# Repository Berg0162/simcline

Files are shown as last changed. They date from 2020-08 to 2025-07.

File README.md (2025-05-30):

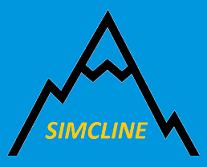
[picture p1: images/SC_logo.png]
SIMCLINE Icon
#  &nbsp; SIMCLINE for Smart TACX, Wahoo KICKR and FTMS enabled trainers
# Simulation of Changing Road Inclination for Indoor Cycling<br>
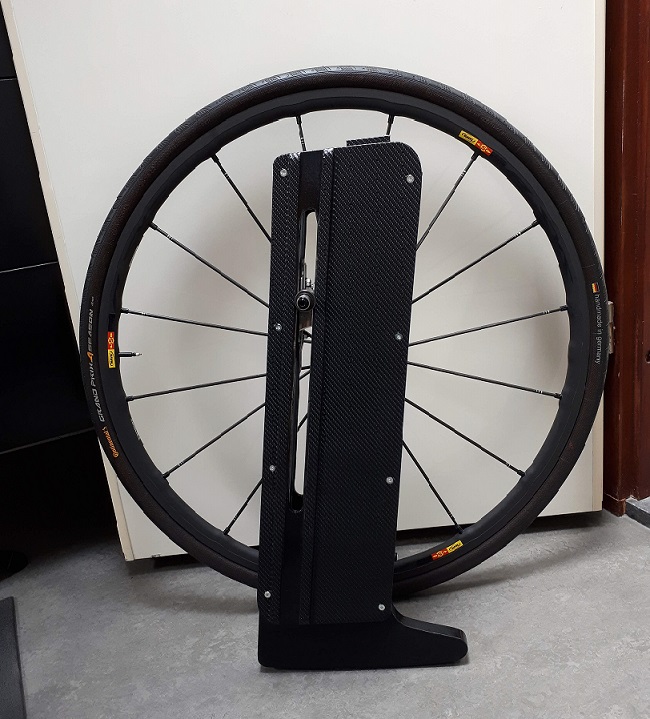
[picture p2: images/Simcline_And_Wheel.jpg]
SIMCLINE 1

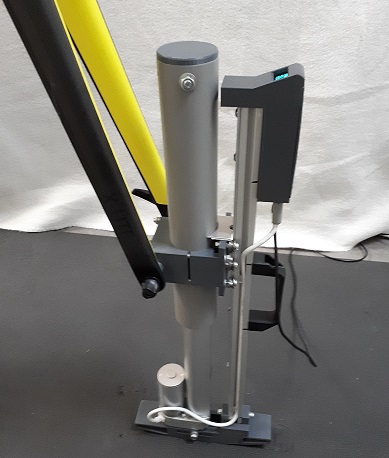
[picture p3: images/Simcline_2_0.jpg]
SIMCLINE 2

The SIMCLINE physically adjusts the bike position to mimic hilly roads, climbing and descending. This allows the rider to naturally change position on the bike, engage climbing muscles, and improve pedaling technique to become a more efficient and powerful climber.<br>
Without user intervention the SIMCLINE will replicate inclines and declines depicted in (online & offline) training programs (like <b>Zwift, Rouvy, VeloReality, myWhoosh</b> and many others) that adjust accordingly the resistance of the indoor trainer.<br>
The SIMCLINE auto connects at power up with a smart Wahoo KICKR trainer or a smart TACX trainer and let's relive the ascents and descents from favorite rides or routes while training indoors.<br>
The physical reach is: 20% maximum incline and -10% maximum decline. However, the reach that the rider is comfortable with can be adjusted!<br>
The SIMCLINE pairs directly to the smart trainer and with your PC/Laptop with (Zwift) training App for a connection that notifies the SIMCLINE to simulate autonomous the (change in) physical grade of the road during an indoor ride.<br>
During operation an OLED display shows the road grade in digits and in graphics.<br>
The SIMCLINE Companion App (for Android smartphones) can be paired, only when the training App is disconnected, for adjusting operational settings, like Ascent Grade Limit (between 0-20%), Descent Grade Limit (between 0-10%), Road Grade Change Factor (between 0-100%) and manual Up and Down control. Notice that the Companion App has a slightly different functionality depending of what brand of trainer (TACX or Wahoo) is connected, due to specific connectivity differences. <br clear="left"> 
<br>
There are <b>Instructables</b> available with all the nitty gritty of how to create, construct and install the various parts and components of the different SIMCLINE versions.<br>

# [Mechanical SIMCLINE version 1.0](https://www.instructables.com/id/SIMCLINE-Simulation-of-Changing-Road-Incline-for-I/)<br>
# [Mechanical SIMCLINE version 2.0](https://www.instructables.com/SIMCLINE-20-Easy-Simulation-of-Road-Incline/)<br>

The applied electronic components in the 2 projects are somewhat different but NOT in an essential way, as documented hereafter.<br>
<b>NOTICE that the SIMCLINE control code can be run with both (mechanically different) SIMCLINE versions!</b> However, 3 different code versions are specially designed for operating with a TACX <b>or</b> Wahoo Kickr <b>or</b> FTMS enabled trainers!</b> You will find in the arduino folder all the test programs and the common libraries. These will help you to test the electronic components separately and built together of both SIMCLINE versions.<br> 

Finally you have to select the SIMCLINE code that is appropriate for the trainer of your liking!<br>

# [nRF52/ESP32 support for Legacy Smart TACX trainers](https://github.com/Berg0162/simcline/tree/master/Tacx%20Smart)<br>

# [nRF52/ESP32 support for Legacy Wahoo KICKR trainers](https://github.com/Berg0162/simcline/tree/master/Wahoo%20Kickr/)<br>

# [nRF52 support for Modern FTMS enabled trainers](https://github.com/Berg0162/simcline/tree/master/FTMS%20Enabled/)<br>

# [ESP32 support for Modern FTMS enabled trainers: Simcline-V2](https://github.com/Berg0162/Simcline-V2)<br>

# Mechanical SIMCLINE 1.0<br>
See: Instructables [SIMCLINE 1.0 Instructables](https://www.instructables.com/id/SIMCLINE-Simulation-of-Changing-Road-Incline-for-I/)
<br clear="left">

# Electronic Components and Circuitry used in version 1.0<br>
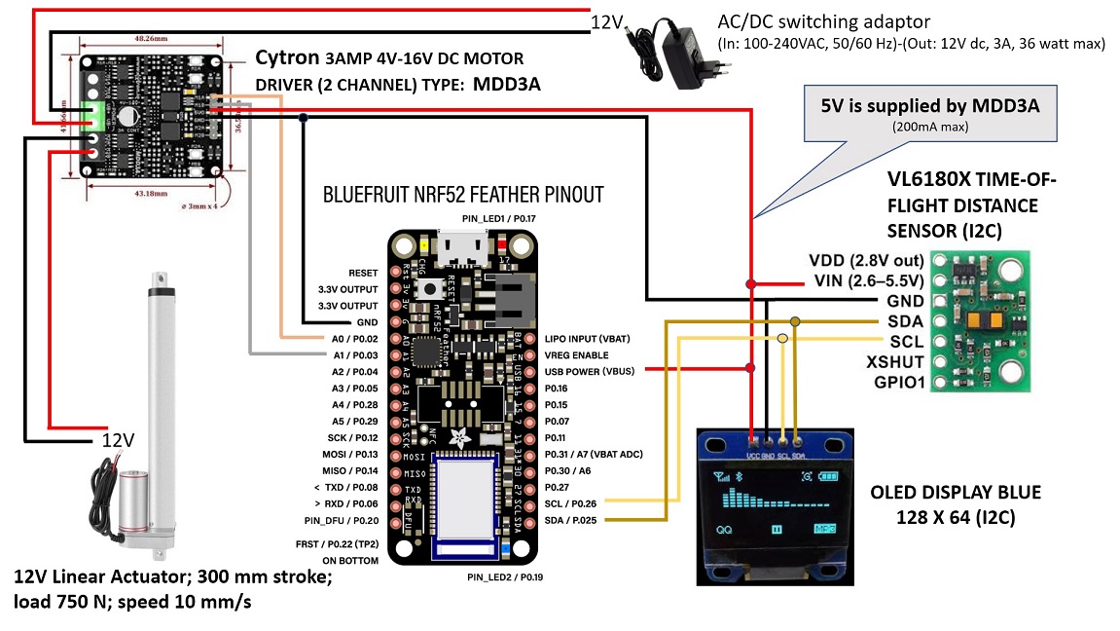
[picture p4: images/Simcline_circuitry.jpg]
Circuitry version 1.0

The original project has been elaborated with different electronic parts than the later version. I have then chosen for the following 4 active components: <br>
<b>Cytron Motor Driver MDD3A.</b> Two channel motor driver for 12 V and 3 Amperes with buttons to test manually the working of the attached DC motor. This board enables the processor to set the Actuator motor in up or down movement. It transforms logical digital levels (Go Up, Go Down and Stop) from the Feather nRF52/ESP32 to switching of 12 Volt at 3 Amperes max., the levels at which the Actuator works.<br>
<b>Adafruit Feather nRF52840 Express</b><br>
Is another easy-to-use all-in-one Bluetooth Low Energy board with a native-Bluetooth chip, the nRF52840! Notice that the Feather nRF52840 Express is to be prefered and has better value for money! It's Adafruits's take on an 'all-in-one' Arduino-compatible + Bluetooth Low Energy with built in USB and battery charging. It is a low power, handsome and fast processor board with lots of memory and I/O pins. Can easily be programmed over the USB connection. <br>
<b>Adafruit HUZZAH32 ESP32 Feather V2</b><br>
Recently we have shared Simcline code that is targeted for another of the Adafruit star Feathers: the <b>Adafruit HUZZAH32 ESP32 Feather V2</b> - with the fabulous ESP32 WROOM module. The ESP32 has both WiFi and Bluetooth Classic/LE support. The new HUZZAH32 V2 is Adafruit's redesigned ESP32-based Feather V2. Compared to the original Feather with only 4 MB Flash and no PSRAM, the V2 has 8 MB Flash and 2 MB PSRAM. Packed with everything people love about Feathers: built in USB-to-Serial converter, automatic bootloader reset, Lithium Ion/Polymer charger, and just about all of the GPIOs brought out.<br>
The programmed Feather nRF52/ESP32 is communicating with (a) the trainer to collect power output  information and (b) with the training App for resistance settings (like grade) or (c) with the Companion App on your mobile phone. The programmed Feather nRF52/ESP32 is in full control of the Simcline operation.<br>

<b>OLED display blue 128x64 pixels</b><br>
Small display with screen of: 25 mm x 19 mm. Shows cycling data and diagnostic info that is gathered during operation by the programmed Feather nRF52/ESP32 to inform the Simcline user about relevant information. NOTICE: Install Straight Pin Through Hole Male PCB Header on the board; these will allow later flat mounting of the board on top of the frame!<br>
<b>Time-of-Flight-Distance sensor VL6180X</b><br>
The sensor contains a very tiny laser source, and a matching sensor. The VL6180X can detect the "time of flight", or how long the laser light has taken to bounce back to the sensor. Since it uses a very narrow light source, it is perfect for determining distance of only the surface directly in front of it. The sensor registers quite accurately the (change in) position of the wheel axle during operation, by measuring the distance between the top of the inner frame and the reflection plate that is mounted on the carriage. The distance feedback of the sensor is crucial for determining how to set the position of the carriage and axle in accordance with the grade information that for example Zwift is using to set the resistance of the trainer. NOTICE: Install Right Angle Through Hole Male PCB Header Pins on the board.<br>
In retrospect I do not regret the component choices made. All components are documented very well. There are lots of examples for use in an Arduino enviroment. They have turned out to be very reliable.<br clear="left">

# Mechanical SIMCLINE 2.0<br>
See: Instructables [SIMCLINE 2.0 Instructables](https://www.instructables.com/SIMCLINE-20-Easy-Simulation-of-Road-Incline/)
<br clear="left">

# Electronic Components and Circuitry used in version 2.0<br>
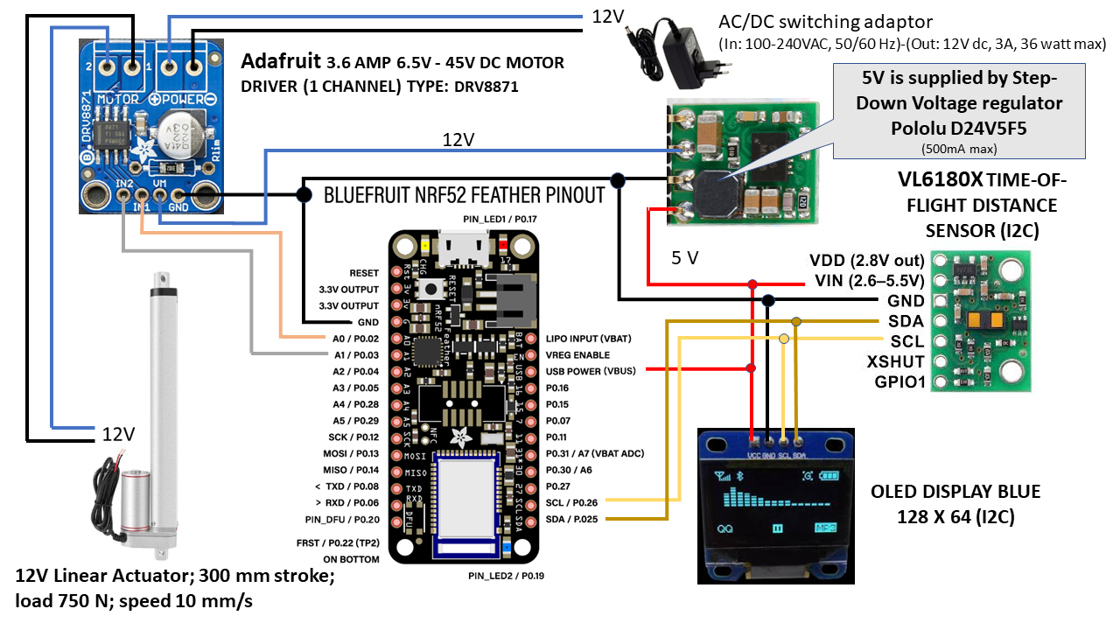
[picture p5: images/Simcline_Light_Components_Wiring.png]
Circuitry version 2.0

I have chosen for the following 5 compact active components that are slightly different from the earlier SIMCLINE project and that can finally all be mounted inside the components box:<br>
<b>Adafruit DRV8871 DC Motor Driver</b><br>
A small one channel motor driver for 12 V (6.5 - 48 V) and 3,6 Amperes max. This board enables the processor to set the Actuator motor in up or down movement. It transforms logical digital levels (Go Up, Go Down and Stop) from the Feather nRF52/ESP32 to switching of 12 Volt at 3,6 Amperes max., the levels at which the Actuator works. Notice that default the board comes limited to 2,6 Amperes and you need to add a resistor to set for max current level. Install Vertical Through Hole Male PCB Header Pins on the board; this will allow correct mounting of the board inside the components box!<br>
<b>Adafruit Feather nRF52840 Express</b><br>
Is another easy-to-use all-in-one Bluetooth Low Energy board with a native-Bluetooth chip, the nRF52840! Notice that the Feather nRF52840 Express is to be preferred and has better value for money! It's Adafruit's take on an 'all-in-one' Arduino-compatible + Bluetooth Low Energy with built in USB and battery charging. It is a low power, handsome and fast processor board with lots of memory and I/O pins. Can easily be programmed over the USB connection.<br>
<b>Adafruit HUZZAH32 ESP32 Feather V2</b><br>
Recently we have shared Simcline code that is targeted for another of the Adafruit star Feathers: the <b>Adafruit HUZZAH32 ESP32 Feather V2</b> - with the fabulous ESP32 WROOM module. The ESP32 has both WiFi and Bluetooth Classic/LE support. The new HUZZAH32 V2 is Adafruit's redesigned ESP32-based Feather V2. Compared to the original Feather with only 4 MB Flash and no PSRAM, the V2 has 8 MB Flash and 2 MB PSRAM. Packed with everything people love about Feathers: built in USB-to-Serial converter, automatic bootloader reset, Lithium Ion/Polymer charger, and just about all of the GPIOs brought out.<br>
The programmed Feather nRF52/ESP32 is communicating with (a) the trainer to collect power output  information and (b) with the training App for resistance settings (like grade) or (c) with the Companion App on your mobile phone. The programmed Feather nRF52/ESP32 is in full control of the Simcline operation.<br>

<b>OLED display blue/white 128x64 pixels (0,96 Inch, I2C)</b><br>
Small display board has a critical overall board size of 25 mm * 27 mm (!); (See for example: [Webshop](https://www.pcboard.ca/oled-128x64)). Display area itself is: 25 mm x 14 mm. Shows cycling data and diagnostic info that is gathered during operation by the Feather nRF52/ESP32 to inform the SIMCLINE user about relevant information. NOTICE: a) Many different formfactors are offered at webshops; b) Install Vertical Through Hole Male PCB Header Pins on the board; this will allow correct mounting of the board inside the components box!<br>
<b>Pololu Time-of-Flight-Distance sensor VL6180X</b><br> The sensor board (12.7 * 17.8 mm) contains a very tiny laser source, and a matching sensor. The VL6180X can detect the "time of flight", or how long the laser light has taken to bounce back to the sensor. Since it uses a very narrow light source, it is perfect for determining distance of only the surface directly in front of it. The sensor registers quite accurately the (change in) position of the wheel axle during operation, by measuring the distance between the top of the inner frame and the reflection plate that is mounted on the carriage. The distance feedback of the sensor is crucial for determining how to set the position of the carriage and axle in accordance with the grade information that for example Zwift is using to set the resistance of the trainer. NOTICE: a) VL6180X boards are also offered by different suppliers and have different formfactors; b) Install Straight Angle Through Hole Male PCB Header Pins on the board; this will allow later flat mounting of the sensor board in the components box!<br>
<b>Pololu D24V5F5</b><br>
This is a small 5V, 500mA Step-Down Voltage Regulator that is responsible for voltage conversion from 12V to 5V, the power supply for all components boards. NOTICE: Install Straight Angle Through Hole Male PCB Header Pins on the board; this will allow later easy mounting of the sensor board in the components box!<br>

All components are documented very well and are low cost. There are lots of examples for use in an Arduino environment. They have turned out to be very reliable. The exact wiring of the components can be followed in the figure above.<br>

# How Zwift, Trainer and Simcline are handling (changes in) road grade during your ride!<br>
1) The trainer calculates the resistance, among others using road grade information. That's why Zwift sends modified road grades to the trainer to set resistance. Simple as that! However, resistance (i.e. road grade) is also dependent of Zwift's famous difficulty setting. With the default difficulty setting of 50%, Zwift sends only half the value of the road grade to the trainer. Only when the Zwift App difficulty setting is 100%, Zwift will send unmodified road grades to the trainer (WYSIWYG). As a consequence the Simcline will lift accordingly and show the road grade values on the display! If you observe deviations when riding long and steady climbs, like Alpe-de-Huez or Mt-Ventoux, check the Zwift App "difficulty setting" that is most likely the cause! Most Zwifters have set the Zwift difficulty at 100%, because they want a "road-realistic" experience when training and racing indoors with Zwift.
2) Trainers do NOT react momentarily, but delayed on changes in road grade, they need to process incoming info and the (direct) drive mechanism has to be settled accordingly before you will feel it as a change in resistance. The delay between the initial command (by Zwift) and the feel on the bike is 1 to 1.5 seconds. To accommodate for this delay, the Zwift app sends commands 1 to 1.5 second <b>earlier</b> (!) than what you observe on your screen (slope of the road you see and the displayed road grade value on the Zwift window). This explains temporarily deviating values on the Simcline display in comparison what you see on the Zwift window, after all Simcline is a MITM and is the first to receive changes in road grade, to react (moving the lift mechanism) and to show the new value on the display. When riding rolling hills in rapid succession, like Zwift's Titans Grove, this is most visible! Notice that the Simcline's responsiveness is benefiting of the feature!
3) Zwift handles downhill roads differently! When the road grade values become negative, during a downhill section of the road, Zwift will consequently send only half of the road grade value to the trainer (i.e Simcline). Modern trainers with direct drive are capable to accelerate proportionally with negative road grades. So when the Zwift window shows a -8.0 grade value it has sent only -4.0 road grade to the trainer. The rationale behind this is to minimize effortless riding, after all you get on an indoor bike to do some work! Simcline will act accordingly and display only 50% of the Zwift road grade value on downhill sections!  
4) After Zwift has paired with your trainer it sends a first road grade value (randomly between 2.0 and 5.0) to the trainer, to wake-up/activate the resistance mechanism. You will feel the resistance while you were expecting a flat road for a start. Simcline, being a MITM, will lift your front wheel accordingly! This road grade value remains constant, until you have actually <b>started</b> with the ride of your choice!
5) The Simcline code has its own setting that influences how it will react on and display the road grade value sent by Zwift. The Grade-Change-Factor functionality was originally designed and implemented to allow a Simcline user to attenuate the actuator movements in case of a noisy and/or slow actuator. Notice that the original (unmodified) Zwift grade value is passed on to the trainer, so the trainer's resistance is NOT affected by the Grade-Change-Factor setting! Default code setting for the Grade-Change-Factor is 100% and it can be modified dynamically using the Simcline app.

In conclusion when you see different road grade values in the Zwift window compared with the Simcline display, this can have different reasons! If you consider this a problem: check first Zwift difficulty setting and Grade-Change-Factor of the Simcline, these can be modified to what you prefer! Like it or not, the other causes are Zwift features and part of the design! Cycling Apps like Rouvy and MyWhoosh handle road grades more or less comparably.

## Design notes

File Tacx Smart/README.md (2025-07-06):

# SIMCLINE Icon &nbsp; SIMCLINE for TACX
# Simulation of Changing Road Inclination for Indoor Cycling <br>
SIMCLINE
SIMCLINE 2
The SIMCLINE physically adjusts the bike position to mimic hilly roads, climbing and descending. This allows the rider to naturally change position on the bike, engage climbing muscles, and improve pedaling technique to become a more efficient and powerful climber.<br>
Without user intervention the SIMCLINE will replicate inclines and declines depicted in (online & offline) training programs (like Zwift, Rouvy, VeloReality and many others) that adjust accordingly the resistance of the indoor trainer.<br>
The SIMCLINE auto connects at power up with a smart TACX trainer and let's relive the ascents and descents from favorite rides or routes while training indoors.<br>
The physical reach is: 20% maximum incline and -10% maximum decline. However, the reach that the rider is comfortable with can be adjusted even during a ride!<br>
The SIMCLINE pairs directly to the TACX smart trainer for a connection that notifies the SIMCLINE to simulate autonomous the (change in) physical grade of the road during an indoor ride.<br>
During operation an OLED display shows the road grade in digits and in graphics or cycling data from the trainer (speed, power, cadence, elapsed time and distance).<br>
The SIMCLINE Companion App (for Android smartphones) can be paired simultaneously for adjusting operational settings, like Ascent Grade Limit (between 0-20%) and Descent Grade Limit (between 0-10%), Road Grade Change Factor (between 0-100%) and the type of OLED display format.<br clear="left"> 

# Choose a Development board: nRF52840 or ESP32?<br>
Until early 2023 the Simcline project (a.o.) solely worked with the <b>Feather nRF52840 Express</b> development board and the Bluefruit/Adafruit libraries. This is a very stable platform and gave reliable results during development and what's more during many indoor seasons of 5 hours per week operation! However, the MITM application and actuator control (a.k.a. Simcline) is at the capacity limits of the nRF52840 processor. 
See for a reliable and <b>proven</b> solution: [Adafruit Feather nRF52840 Express](https://learn.adafruit.com/introducing-the-adafruit-nrf52840-feather) <br>

So the question was raised why not use the <b>ESP32</b>, a series of low-cost and low-power System on a Chip (SoC) microcontrollers developed by Espressif that include Wi-Fi and Bluetooth wireless capabilities and dual-core processor? See for an introduction: [Random Nerds Tutorials](https://randomnerdtutorials.com/getting-started-with-esp32/). Particularly the multiprocessing capabilities of the dual-core processor make the ESP32 a very tempting option in this project!
To benefit of the same formfactor (fit with the Simcline 2.0 component box!), I decided to (re)produce the Simcline code with the [Adafruit Feather ESP32 V2](https://learn.adafruit.com/adafruit-esp32-feather-v2) for the <b>ESP32</b> platform. Just comparing the overal specs (on paper) of both processor platforms is not sufficient... one needs to take into account the (quality of the) available libraries as well to reach success. The 'standard' ESP32 Arduino <b>Bluedroid</b> library (for BLE support) turned out to be buggy! Fortunately [H2Zero](https://github.com/h2zero/NimBLE-Arduino) has created a more or less compatible replacement for Bluedroid, called <b>NimBLE-Arduino</b>! The application of <b>NimBLE</b> saved the porting of the software to the ESP32 platform! 
In week 10 of 2023 the ESP32 code reached a stable level and became publicly available for testing with Tacx-trainers.

# How to start?<br>
+ Install the [Arduino IDE](https://www.arduino.cc/en/Main/Software) and all the libraries on a PC/Mac.
+ If you are using an ESP32 board then also download the ESP32 NimBLE library, see [Arduino Installation NimBLE](https://github.com/h2zero/NimBLE-Arduino#arduino-installation)
+ Download all the code from [Github](https://github.com/Berg0162/simcline/tree/master/Tacx%20Smart) and install.
<br>
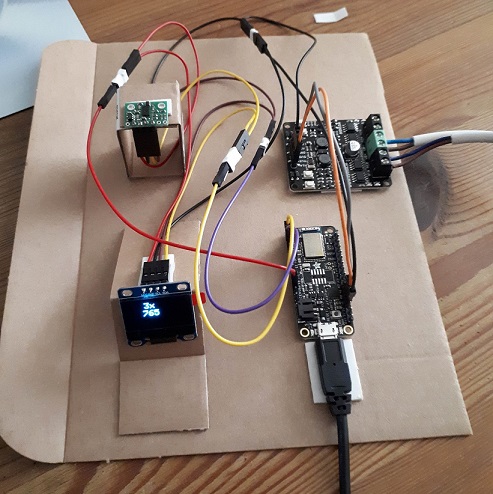
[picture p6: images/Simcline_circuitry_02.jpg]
Cardboard

When I started the project in 2020 I did not have any practical experience with any of the components. So I had to setup the circuitry step by step adding components and did a lot of time consuming but instructive testing first. My advice is to setup the electronic components first in a similar way as shown on the photo with the cardboard base. Use double sided adhesive tape but only attach it on sections that have no pcb-wiring or soldering, to avoid possible electrical interference. You will find in this Github repository all the code that controls the Simcline and the Arduino test programs (modified for this project) that focus on components seperately and in conjunction.<br clear="left">

# ANT+, FE-C protocol and BLE<br>
It took me a lot of time exploring the relevant techniques, protocols and software tools involved with ANT+, BLE and FE-C to acquire the approriate knowledge. Many projects at Github address ANT+ and/or BLE with a different point of departure, however I have learnt a lot of looking closely at the many program codes, explanations and descriptions. Finally, I tracked down how a smart up/down lift of my front wheel axle is optimally benefitting from the (ANT+) FE-C protocol when I am indoor riding with the TACX Neo in the hilly Zwift game world or with any other virtual cycling program that simulates road grade. After a succesfull proof of concept with ANT+ and BLE tools (see [ThisisANT Tools](https://www.thisisant.com/developer/resources/software-tools/) and [Nordic NRF Connect](https://www.nordicsemi.com/Software-and-tools/Development-Tools/nRF-Connect-for-mobile). I was convinced to bring the project to a successful conclusion!
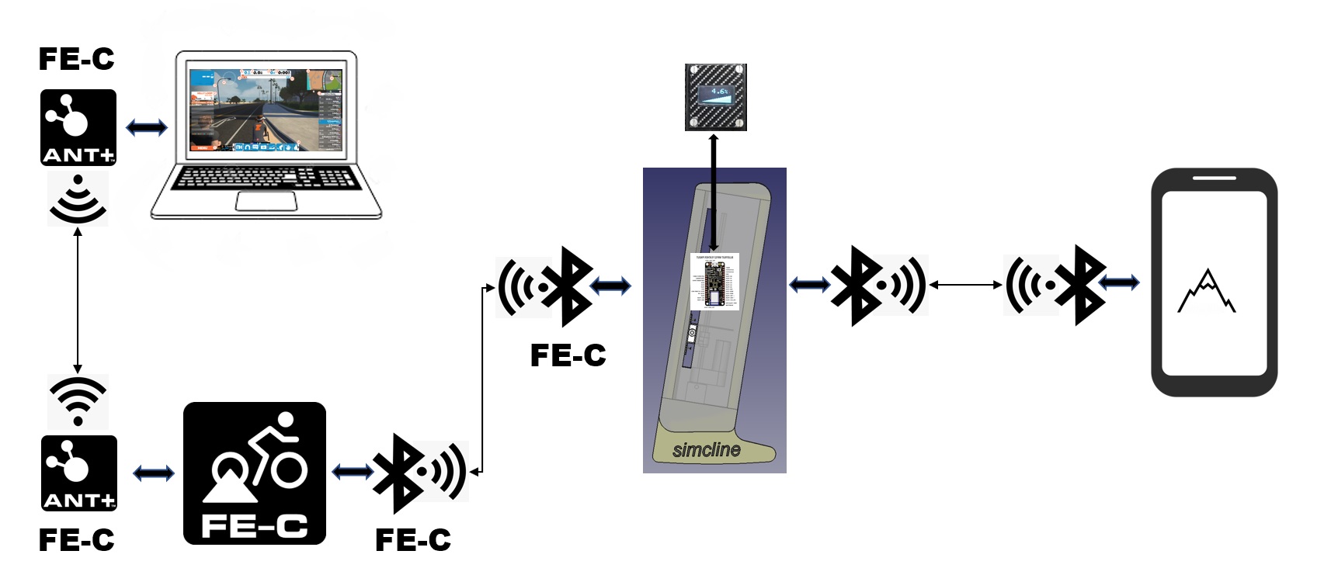
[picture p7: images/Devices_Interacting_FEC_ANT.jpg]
FE-C
<br clear="left">
<b>ANT+ Trainer Control (FE-C)</b><br>
The ANT+ FE-C protocol details the bi-directional message communication of trainer data (speed, power, etcetera) from trainer to the controller and from the controller to the trainer commands or settings of targeted power, trainer resistance (grade) and calibration controls. See [ThisisAnt](http://www.thisisant.com/) for all conceivable documentation, tools, implementations, ANT+ based products, etcetera! See at Github for a detailed description of the [ANT Message Protocol and Usage](https://github.com/Berg0162/simcline/blob/master/docs/ANT_Message_Protocol_and_Usage_Rev_5.1.pdf).
The majority of FE-C trainers on the market is dual ANT+ & Bluetooth Smart in some capacity. The Tacx Neo generation has full capacity: ANT+ Trainer Control (FE-C) and Bluetooth Smart.<br>
Tacx published in 2015 a document [TACX, FE-C and Bluetooth](https://github.com/Berg0162/simcline/blob/master/docs/How_to_FE_C_over_BLE_v1_0_0.pdf) that explains how to use the FE-C ANT+ protocol over BLE feature implemented on all Tacx Smart Trainers then: `Genius Smart, Bushido Smart, Vortex Smart, Flow Smart, Satori Smart and NEO`. Tacx designed this feature because at that time an open standard (on BLE) for trainers was lacking. <b>Always check if your trainer has support for the FE-C ANT+ protocol over BLE feature, since NOT all TACX Smart Trainers that are labelled smart are equally smart!</b>
Now there is (<b>FTMS</b>) FiTness Machine Service protocol to control fitness equipment over Bluetooth. According to the smart trainer recommendations guide winter 2019-2020 of [DCRainmaker](https://www.dcrainmaker.com/2019/10/the-smart-trainer-recommendations-guide-winter-2019-2020.html) the situation evolved:
> Meanwhile, for Bluetooth Smart, there’s FTMS, which is basically the same thing as FE-C when it comes to trainers. It’s not quite as widely adopted yet by trainer companies, but is by app companies. On the trainer company side only Elite, Saris, and Kinetic support it across the board. With Tacx having it on some but not all units, and Wahoo having it on no units (but all Wahoo and Tacx trainers support private Bluetooth Smart with all major apps anyway).<br>

<b>FE-C over Bluetooth</b><br>
In the document Tacx described how Tacx Smart trainers use an ANT+ FE-C definition for the data content, but transports this data over a BLE serial port service. The prerequisite that remains for this technique is thourough knowledge of ANT+ <b>AND</b> the ANT+ FE-C protocol. A complete description of FE-C can be found here at [Github](https://github.com/Berg0162/simcline/blob/master/docs/ANT+_Device_Profile_Fitness_Equipment_Rev_5.0.pdf).<br>
<b>Nordic Serial Port Service</b><br>
The transport method that is used is derived from the Nordic Uart Service. This serial port service can basically send and receive arrays of data ranging from 1..20 bytes. The only difference is the service UUID and the two characteristics UUID’s. These are renamed conforming the internal Tacx standard UUID with the specific part for the FE-C service starting with 0xFEC.<br>
<b>ANT+ and BLE Roles</b><br>
The Adafruit Feather nRF52 Express is equiped with a native-Bluetooth chip, the nRF52840 of Nordic Semiconductor. This chip can be loaded with "SoftDevices" for different applications. Nordic nRF52 and nRF51 Series support ANT+ and ANT+ / Bluetooth LE SoftDevices. However, the adafruit version is loaded with SoftDevice S132: a high-performance Bluetooth Low Energy protocol stack for the nRF52840 System-on-Chips (SoCs). It supports up to 20 concurrent links in all roles (Broadcaster, <b>Central</b>, Observer, <b>Peripheral</b>). It is Bluetooth 5.1 qualified and supports the following Bluetooth features: high-throughput 2 Mbps, Advertising Extensions and channel selection algorithms. <br>
> Recently we have shared Simcline code that is targeted for another of the Adafruit star Feathers: the <b>Adafruit HUZZAH32 ESP32 Feather V2</b> - with the fabulous ESP32 WROOM module. The ESP32 has both WiFi and Bluetooth Classic/LE support. The new HUZZAH32 V2 is Adafruit's redesigned ESP32-based Feather V2. Compared to the original Feather with only 4 MB Flash and no PSRAM, the V2 has 8 MB Flash and 2 MB PSRAM. Packed with everything people love about Feathers: built in USB-to-Serial converter, automatic bootloader reset, Lithium Ion/Polymer charger, and just about all of the GPIOs brought out.<br>

In our design the SIMCLINE has a <b>Central</b> and as well as a <b>Peripheral</b> role simultaneously. The communication SIMCLINE to Trainer is Central to Peripheral respectively and the communication SIMCLINE to Smartphone is Peripheral to Central. The peripheral BLE Device is advertising its name, services and characteristics and the central device is deciding to connect and control the communication. <br>
The communication between the trainer (<b>controllable</b>) and the PC/MAC/Tablet-application (<b>controller</b>, like Zwift) is full blown ANT+ and complies the FE-C protocol. The SIMCLINE is not interfering with this setup in any way! The application on PC/MAC/Tablet is <b>controller</b> and remains in full and only charge of setting the trainers resistance.<br>
<b>How to detect the grade of the simulated track?</b><br>
The SIMCLINE is paired with the trainer over a different channel: Bluetooth! In that configuration it is complying to the ANT+ FE-C protocol as well but over Bluetooth LE. The trainer is not only broadcasting FE-C messages with cycling data (speed, cadence, power, etcetera) over ANT+ to the <b>controller</b>-application (like Zwift), but also over the BLE connection to the paired Feather nRF52/ESP32. The program of the Feather nRF52/ESP32 is dealing with these data in its own way, independent of the <b>ANT+ controller</b>-application.
At regular intervals the Feather nRF52/ESP32 is programmed to send a socalled Common Page 70 (0x46) (Request Data Page) with the request data page field set to Data Page <b>51</b>.
```C++
.
//Define the FE-C ANT+ Common Page 70 with Request for Page #51
const unsigned char Page51Bytes[13] = {
    0xA4, //Sync
    0x09, //Length
    0x4F, //Acknowledge message type
    0x05, //Channel 
          //Data
    0x46, //Common Page 70
    0xFF,
    0xFF,
    0xFF, //Descriptor byte 1 (0xFF for no value)
    0xFF, //Descriptor byte 2 (0xFF for no value)
    0x80, //Requested transmission response
    0x33, //Requested Page number 51 
    0x01, //Command type (0x01 for request data page, 0x02 for request ANT-FS session)
    0x47}; //Checksum;
.
```
Sending Common Page 70 allows a connected device to request specific data pages from the trainer. The trainer replies with Common Page 71 (0x47) (Command Status) to the requester, the Feather nRF52/ESP32. The purpose of the command status page is to confirm the status of commands (and settings) sent from a controller to the controllable trainer. The last <b>settings</b> of the Data Page 51 (0x33) (Track Resistance) are included in the data of Common Page 71. The Track Resistance Page itself is sent by the controller (like Zwift) to command the trainer to use simulation mode, and to set the desired track resistance factors. It provides the simulation parameters for the trainer, the rolling resistance and gravitational resistance applied to the rider. <br>
```C++
.
#endif
  // Standard FE-C Data Message Format
  // buffer[0]  ->  Sync
  // buffer[1]  ->  Msg Length
  // buffer[2]  ->  Msg ID
  // buffer[3]  ->  Channel Number
  // buffer[4]-buffer[12] Payload of 8 bytes --> buffer[4] is byte(0) of Payload bytes 
  // buffer[13] ->  Checksum
  // --------------------------------
  uint8_t DataPageNumber = buffer[4]; // Get Data Page Number from ANT FE-C packet
  // process only the data pages we are interested in, ignore others !
  switch(DataPageNumber) {
    ///////////////////////////////////////////////////////////////
    //////////////////// Handle PAGE 71 ///////////////////////////
    ////////////// Requested PAGE 51 for grade info ///////////////
    //At a regular rate Page 51 is requested for, so process here//
    ///////////////////////////////////////////////////////////////
    case 0x47 :
    // buffer[4] -> Contains 71 (0x47) -> Common Page 71 -> Command status
    // buffer[5] -> Last Received Command ID
    // buffer[6] -> Sequence #
    // buffer[7] -> Command Status
    // buffer[8]-buffer[12] -> Response data 5 bytes
    // buffer[13] -> Checksum
    if ( buffer[5] == 0x33 ) { // check for Requested Page 51
      // We are interested in the Requested Page 51 (0x33) --> Track Resistance
      // in that case the packet contains:
      // buffer[5] -> Last Received Command ID --> Data Page Number 51 (0x33)
      // buffer[6] -> Reserved and set to 0xFF
      // buffer[7] -> Reserved and set to 0xFF
      // buffer[8] -> Reserved and set to 0xFF
      // buffer[9]-buffer[12] -> Response data 4 bytes
      // buffer[13] -> Checksum
      uint8_t lsb_GradeValue = buffer[9]; // Grade (Slope) LSB
      uint8_t msb_GradeValue = buffer[10];// Grade (Slope) MSB
      RawgradeValue = lsb_GradeValue + msb_GradeValue*256;
      // buffer[11] -> Coefficient of Rolling Resistance
.
```
By sending regularly a request for Data Page 51 (0x33) (Track Resistance) the SIMCLINE is always informed about the settings of the current grade of the simulated track and the coefficient of rolling resistance. These values are both set by the <b>ANT+ controller</b>. For proper functioning of the SIMCLINE only the current road grade is critical.</br>

# Dual Processor use with ESP32
One of the advantages of the ESP32 platform is the fact that the ESP32 WROOM processor has two cores. This makes it possible to precisely balance the load of a program over 2 processor cores. <br>
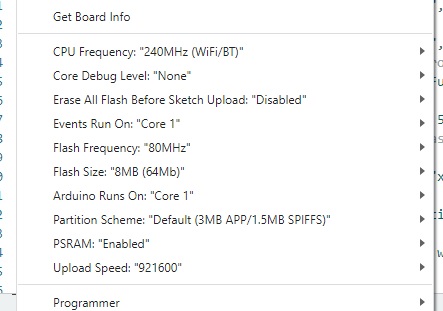
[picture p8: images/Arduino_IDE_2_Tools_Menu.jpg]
Arduino IDE 2.0 Tools Menu

With the Simcline this is particular usefull for the motor control of the actuator. During operation Zwift sends from time to time new settings, and one of these is the grade value (road inclination in degrees). The program translates the grade to a level that should be reached by the actuator to simulate exactly the road grade that was received from Zwift. However, the actuator can only be switched to <b>move up</b>, <b>move down</b> or <b>stop</b>. After  having set the actuator to move (up or down), the program has to check continuously if the actuator has reached the desired level by reading its position with the help of the Time-Of-Flight sensor and act accordingly. Meanwhile the trainer sends your cycling data and the Zwift app has to confirm the receipt of these data. The data sent by Zwift has also to be tranferred to the trainer and also the trainer has to confirm the receipt. Being a MITM means handling a lot of BLE traffic and it does not allow for mistakes!
The load of the Simcline program itself, the BLE handling and the critical control of the actuator is balanced over 2 processor cores on the ESP32 platform.
The following code snippets show how this is achieved for controlling the actuator motor. To avoid conflicts during variable updates (i.c. TargetPosition) a Binary Semaphore scheme is applied to protect <b>task shared variables</b> during an update.<br clear="left">

At the start the major players are defined
```C++
.
// ----------------------xControlUpDownMovement task definitions ------------------
SemaphoreHandle_t xSemaphore = NULL;
TaskHandle_t ControlTaskHandle = NULL;
// Set Arduino IDE Tools Menu --> Events Run On: "Core 1"
// Set Arduino IDE Tools Menu --> Arduino Runs On: "Core 1"
// Run xControlUpDownMovement on "Core 0"
const BaseType_t xControlCoreID = 0;
void xControlUpDownMovement(void* arg); 
// --------------------------------------------------------------------------------
.
```
In the setup() routine the variables are instantiated (after checking the mechanics of the motor function) and the <b>xControlUpDownMovement</b> task is pinned to processor <b>core 0</b>, with a priority of 10. Most of the Simcline program and Events are running on <b>core 1</b>.
```C++
.
  } else {
    ShowOnOledLarge("Testing", "Functions", "Done!", 500);
    // Is working properly --> Start Motor Control Task
    xSemaphore = xSemaphoreCreateBinary();
    xTaskCreatePinnedToCore(xControlUpDownMovement, "xControlUpDownMovement", 4096, NULL, 10, &ControlTaskHandle, xControlCoreID);
    xSemaphoreGive(xSemaphore);
    DEBUG_PRINTLN("Motor Control Task Created and Active!");        
    IsBasicMotorFunctions = true;
    DEBUG_PRINTLN("Simcline Basic Motor Funtions are working!!");
    // Put Simcline in neutral: flat road position
#ifdef EMA_ALPHA
    // Init EMA filter at first call with flat road position as reference
    TargetPosition = EMA_TargetPositionFilter(TargetPosition); 
#endif
    SetNewActuatorPosition();
  }
.
```
Whenever new values for the road grade are received these are translated to a physical actuator position (level above ground) and the <b>TargetPosition</b> is set during Semaphore protection. When the new position has been set, the protection is cancelled, and the motor control task can access the new setting.
```C++
.
void SetNewActuatorPosition(void) {
  // Handle mechanical movement i.e. wheel position in accordance with Road Inclination
  // Map RawgradeValue ranging from 0 to 40.000 on the
  // TargetPosition (between MINPOSITION and MAXPOSITION) of the Lifter
  // Notice 22000 is equivalent to +20% incline and 19000 to -10% incline
  RawgradeValue = constrain(RawgradeValue, RGVMIN, RGVMAX); // Keep values within the safe range
  TargetPosition = map(RawgradeValue, RGVMIN, RGVMAX, MAXPOSITION, MINPOSITION);
  // EMA filter for smoothing quickly fluctuating Target Position values see: Zwift Titan Grove
#ifdef EMA_ALPHA
  TargetPosition = EMA_TargetPositionFilter(TargetPosition);
#endif
  if(IsBasicMotorFunctions) {  
    xSemaphoreTake(xSemaphore, portMAX_DELAY); 
    lift.SetTargetPosition(TargetPosition);
    xSemaphoreGive(xSemaphore);
#ifdef MOVEMENTDEBUG
    DEBUG_PRINTF("RawgradeValue: %05d Grade percent: %03.1f%% ", RawgradeValue, gradePercentValue);
    DEBUG_PRINTF("TargetPosition: %03d\n", TargetPosition, DEC);
#endif
  }  
}
.
```
The motor control task regularly checks how far off the actuator position is from its target position and if it should be braked yet. However, it happens all the time that the road grade changed from upward to flat or to downward. The actuator should follow these changes and therefore the motor is switched many times to brake or to reverse its movement. When the motor control task is accessing the relevant variables the semaphore is protecting these against updates!
```C++
void xControlUpDownMovement(void *arg) {
  // Check "continuously" the Actuator Position and move Motor Up/Down until target position is reached
  int OnOffsetAction = 0;
  const TickType_t xDelay = 110 / portTICK_PERIOD_MS; // Block for 110ms < 10Hz sample rate of VL6180X
  while(1) {
    if(xSemaphoreTake(xSemaphore, portMAX_DELAY)) {
        // BLE channels can interrupt and consequently target position changes on-the-fly !!
        // We do not want changes in TargetPosition during one of the following actions!!!
        OnOffsetAction = lift.GetOffsetPosition(); // calculate offset to target and determine action
        switch (OnOffsetAction)
            {
              case 0 :
                lift.brakeActuator();
                #ifdef MOVEMENTDEBUG
                DEBUG_PRINTLN(F(" -> Brake"));
                #endif
                break;
              case 1 :
                lift.moveActuatorUp();
                #ifdef MOVEMENTDEBUG
                DEBUG_PRINTLN(F(" -> Upward"));
                #endif
                break;
              case 2 :
                lift.moveActuatorDown();
                #ifdef MOVEMENTDEBUG
                DEBUG_PRINTLN(F(" -> Downward"));
                #endif
                break;
              case 3 :
                // Timeout --> OffsetPosition is undetermined --> do nothing and brake
                lift.brakeActuator();
                #ifdef MOVEMENTDEBUG
                DEBUG_PRINTLN(F(" -> Timeout"));
                #endif
                break;
            } // switch 
        xSemaphoreGive(xSemaphore);    
    }      
    vTaskDelay(xDelay);
  } // while
} // end
```

# Overview of Arduino Feather nRF52840 Express Program Code Flow and Snippets<br>
+ Include headers of libraries and declare classes
```C++
.
// Library Adafruit Feather nRF52 Bluefruit (Bluetooth Low Energy)
#include <bluefruit.h>
// Libraries for use of I2C devices (Oled and VL6180X distance sensor)
#include <SPI.h>
#include <Wire.h>
// Necessary libraries for use of Oled display(s)
#include <Adafruit_GFX.h>
#include <Adafruit_SSD1306.h>
// Additional splash screen bitmap and icon(s) for Oled
#include "Adafruit_SSD1306_Icons.h" // needs to be in directory of main code
// Declare the SSD1306 Class
Adafruit_SSD1306 display(SCREEN_WIDTH, SCREEN_HEIGHT, &Wire, OLED_RESET);
#include <avr/dtostrf.h>
// LittleFS for internal storage of persistent data on the Feather nRF52
#include <Adafruit_LittleFS.h>
#include <InternalFileSystem.h>
using namespace Adafruit_LittleFS_Namespace;
// Managing persistence of some data with LittleFile system
// PeRSistent Data  --> PRS data
#define PRS_FILENAME "/prsdata.txt"
// Declare the File Class
File file(InternalFS);
// LittleFS--------------------------------------------------------------
// Library code for low level measuring (VL6180X) and controlling UP and down movement
#include <Lifter.h>
.
```
+ Define variables, set to default values and initialize classes.
```C++
.
// Declare in Reversed order !!!
uint8_t TACX_FEC_PRIMARY_SERVICE_Uuid[16]=     {0x9E, 0xCA, 0xDC, 0x24, 0x0E, 0xE5, 0xA9, 0xE0, 0x93, 0xF3, 0xA3, 0xB5, 0xC1, 0xFE, 0x40, 0x6E,};
uint8_t TACX_FEC_READ_CHARACTERISTIC_Uuid[16]= {0x9E, 0xCA, 0xDC, 0x24, 0x0E, 0xE5, 0xA9, 0xE0, 0x93, 0xF3, 0xA3, 0xB5, 0xC2, 0xFE, 0x40, 0x6E,};
uint8_t TACX_FEC_WRITE_CHARACTERISTIC_Uuid[16]={0x9E, 0xCA, 0xDC, 0x24, 0x0E, 0xE5, 0xA9, 0xE0, 0x93, 0xF3, 0xA3, 0xB5, 0xC3, 0xFE, 0x40, 0x6E,};
.
```
```C++
.
//Declare crucial services and charateristics for TACX FE-C trainer
BLEClientService        fecps(TACX_FEC_PRIMARY_SERVICE_Uuid);
BLEClientCharacteristic fecrd(TACX_FEC_READ_CHARACTERISTIC_Uuid);
BLEClientCharacteristic fecwr(TACX_FEC_WRITE_CHARACTERISTIC_Uuid);
.
```
```C++
// Declaration of Function prototypes
bool getPRSdata(void);
void setPRSdata(void);
void prph_connect_callback(uint16_t conn_handle);
void prph_disconnect_callback(uint16_t conn_handle, uint8_t reason);
void prph_bleuart_rx_callback(uint16_t conn_handle);
void prph_bleuart_TX_Grade(void);
void prph_bleuart_TX_PWR_CAD(void);
void prph_bleuart_TX_ADT_SPD_AET(void);
void scan_stop_callback(void);
void adv_stop_callback(void);
void scan_callback(ble_gap_evt_adv_report_t* report);
void connect_callback(uint16_t conn_handle);
void disconnect_callback(uint16_t conn_handle, uint8_t reason);
void SendRequestPage51(void);
void fecrd_notify_callback(BLEClientCharacteristic* chr, uint8_t* data, uint16_t len);
void SetNeutralValues(void);
bool ControlUpDownMovement(void);
void ShowOnOledLarge(char *Line1, char *Line2, char *Line3, uint16_t Pause);
void BuildBasicOledScreen(void);
void ShowValuesOnOled(void);
void ShowSlopeTriangleOnOled(void);
```
<b>Begin of the Arduino Setup() Function</b><br>
+ Get or set (first time only) the values of relevant and crucial variables to persistence, whith the Companion App the user can set these on the fly!
+ Start the show for the SSD1306 Oled display.
+ Initialize Lifter Class data, variables, test and set to work!
```C++
.
lift.Init(actuatorOutPin1, actuatorOutPin2, MINPOSITION, MAXPOSITION, BANDWIDTH);
.
```
```C++
.
// Test Actuator and VL8106X for proper functioning
ShowOnOledLarge("Testing", "Up & Down", "Functions", 100);
if (!lift.TestBasicMotorFunctions()) {
    ShowOnOledLarge("Testing", "Functions", "Failed!", 500);
    IsBasicMotorFunctions = false; // Not working properly
    }
else {
    ShowOnOledLarge("Testing", "Functions", "Succes!", 500);
    // Is working properly
    IsBasicMotorFunctions = true;
    // Put Simcline in neutral: flat road position
    SetNeutralValues(); // set relevant flat road values
    while (ControlUpDownMovement()) { // wait until flat road position is reached
    }
    }
.    
```
+ Initialize Bluefruit with maximum connections as Peripheral = 1, Central = 1.
```C++
.
  Bluefruit.begin(1, 1);
  Bluefruit.setTxPower(4); // Check bluefruit.h for supported values
  Bluefruit.setName("Bluefruit-nRF52");
.
```
+ Setup Central Scanning for an advertising TACX trainer...
```C++
.
  Bluefruit.Scanner.restartOnDisconnect(true);
  Bluefruit.Scanner.filterRssi(-70);      // original value of -80 , we want to scan only nearby peripherals, so get close to your TACX trainer !!
  Bluefruit.Scanner.setInterval(160, 80); // in units of 0.625 ms
// We are only interested in the services of the TACX Trainer
  Bluefruit.Scanner.filterUuid(TACX_FEC_PRIMARY_SERVICE_Uuid);
  Bluefruit.Scanner.useActiveScan(true);
.    
```
+ Initialize TACX FE-C trainer services and characteristics.
+ Declare Callbacks for Peripheral (smartphone connection) and Callbacks for Central (trainer connection).
```C++
.
// Declare Callbacks for Peripheral (smartphone connection)
  Bluefruit.Periph.setConnectCallback(prph_connect_callback);
  Bluefruit.Periph.setDisconnectCallback(prph_disconnect_callback);

// Callbacks for Central (trainer connection)
  Bluefruit.Central.setDisconnectCallback(disconnect_callback);
  Bluefruit.Central.setConnectCallback(connect_callback);
  Bluefruit.Scanner.setRxCallback(scan_callback);
  Bluefruit.Scanner.setStopCallback(scan_stop_callback);

// set up callback for receiving ANT+ FE-C packets; this is the main work horse!
  fecrd.setNotifyCallback(fecrd_notify_callback);
.    
```
+ Initialize some characteristics of the Device Information Service.
+ All initialized --> Start the actual scanning!
```C++
.
// Show Scanning message on the Oled
  ShowOnOledLarge("Scanning", "for", "Trainer", 500);
  Bluefruit.Scanner.start(300); // 0 = Don't stop scanning or after n, in units of hundredth of a second (n/100)
  while (Bluefruit.Scanner.isRunning()) { // do nothing else but scanning....
  }
.    
```
+ Initialize and setup BLE Uart functionality for connecting to smartphone --> Start the advertising!
```C++
   bleuart.begin();
   bleuart.setRxCallback(prph_bleuart_rx_callback);
// Advertising packet construction
   Bluefruit.Advertising.addFlags(BLE_GAP_ADV_FLAGS_LE_ONLY_GENERAL_DISC_MODE);
   Bluefruit.Advertising.addTxPower();
// Include the BLE UART (AKA 'NUS') 128-bit UUID
   Bluefruit.Advertising.addService(bleuart);
   Bluefruit.Advertising.setStopCallback(adv_stop_callback);
// Start advertising: to be picked up by a Smartphone with the Companion App!
   Bluefruit.Advertising.start(60); // 0 = Don't stop advertising or after n (!) seconds -> 1 minuut
.    
```
<b>End of the Arduino Setup() Function</b><br>

+ The callback functions are dominating completely the processing and <b>loop()</b> would never have been called, since there is a constant stream of FE-C packets that are coming in!
+ The function <b>fecrd_notify_callback</b> does the bulk of the work!
```C++
.
    void loop()
    { // Do not use ... !!!
    }
.
```
+ <b>fecrd_notify_callback</b> is a callback that is triggered when a ANT+ message is sent from TACX Trainer.
```C++
.
  void fecrd_notify_callback(BLEClientCharacteristic* chr, uint8_t* data, uint16_t len) {
// The FE-C Read charateristic of ANT+ packets
// In TACX context receive or send arrays of data ranging from 1--20 bytes so FE-C
// will not exceed the 20 byte maximum...
// Data pages are broadcast (by the trainer) at 4Hz message rate
  uint8_t buffer[20 + 1];
  memset(buffer, 0, sizeof(buffer)); // fill with zero
// Transfer first the contents of data to buffer (array of chars)
  for (int i = 0; i < len; i++) {
    if ( i <= sizeof(buffer)) {
      buffer[i] = *data++;
    }
   }
.   
```
+ All ANT+ FE-C message pages are handled, parsed and relevant variables set to new values.
```C++
// Show the actual values of the trainer on the Oled
  if (OledDisplaySelection == 1) {
    ShowValuesOnOled();
  } else {
    ShowSlopeTriangleOnOled();
  }
// Check and control motor up/down movement within settings!
  if (IsBasicMotorFunctions) {
    while (ControlUpDownMovement()) {
    }
  }
.  
```
+ Send a request for Page 51 about every 4 seconds.

# SIMCLINE Companion App<br>
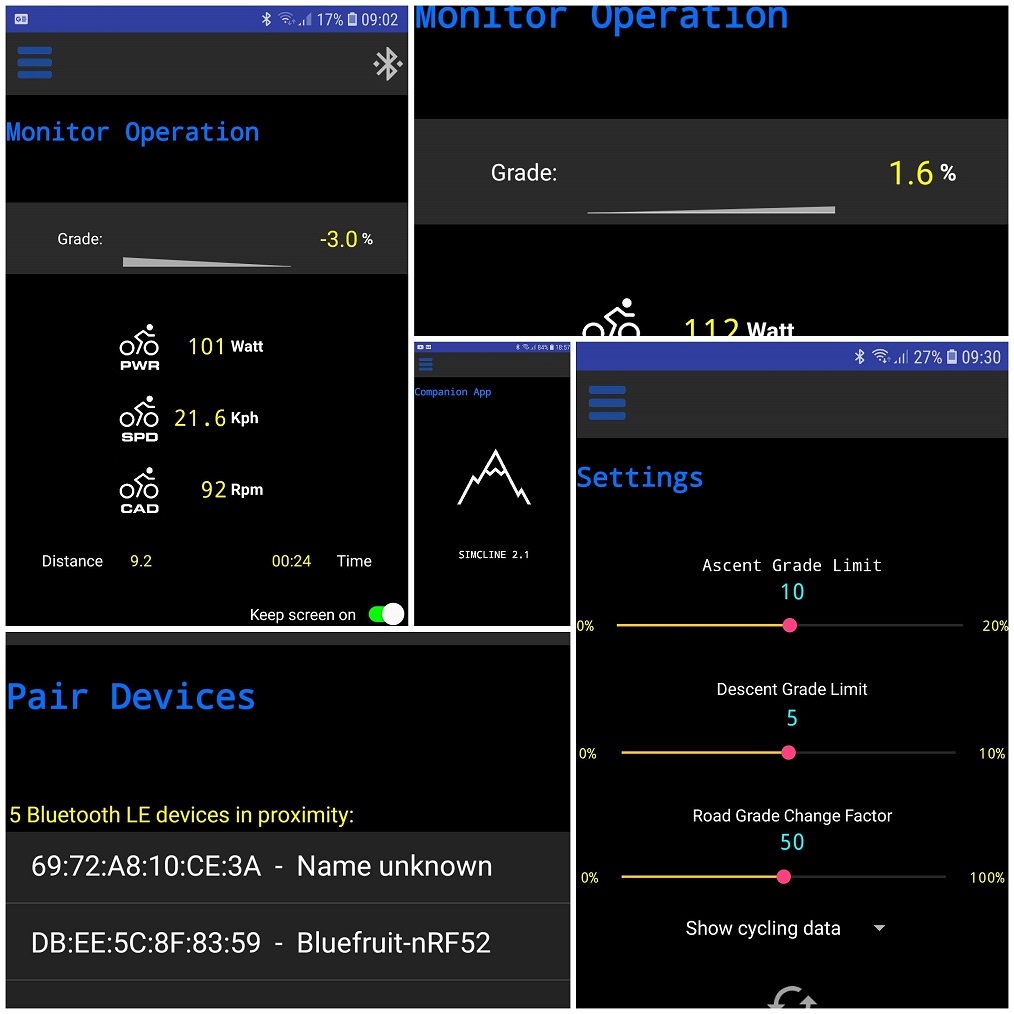
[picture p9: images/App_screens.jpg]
<br clear="left">
After the project was more or less accomplished and running, practical experience was gathered during many months. It became clear to me that a Companion App with some basic features would be very welcome.<br> You need some easy possibility to change settings that in the beginning were supposed to be set at compile time only. Insights change with time! Reprogramming the Arduino code on the Feather over USB becomes cumbersome when the SIMCLINE has to be dismantled every time! Therefore it was decided to develop a Companion App that would allow at minimal a feature for changing settings.<br clear="left">
After some exploring of the field (I had no experience with App development), the outcome was to build one (for Android) in the accessible environment of [MIT App Inventor 2](https://appinventor.mit.edu).<br>
+ Download the <b>MIT App Inventor</b> SIMCLINE Companion App code with extension *file*<b>.aia</b>
+ [Visit at AppInventor](https://appinventor.mit.edu), You can get started by clicking the orange "Create Apps!" button from any page on the website.
+ Get started and upload the SIMCLINE Companion App code.
+ Or upload the SIMCLINE Companion App <b>APK</b> to your Android device directly and install the APK. Android will call this a security vulnerability!

# Flow and Some Code Snippets<br>
+ At startup SIMCLINE starts (BLE) advertising, independent of whether a trainer connection is realized before or not! The Companion App establishes a connection over BLE and the Nordic UART service (a.k.a. BLEUART) for exchange of information is applied. A simple dedicated protocol was implemented that allows for bidirectional exchange of short strings (<= 20 bytes) containing diagnostic messages or cyling variables.<br>
+ At first the SIMCLINE sends the latest (persistent) settings data to allow the App user to assess the current values.
+ The SIMCLINE sends regularly cyling data (like Speed, Power, Cadence, Grade etcetera) that were received from the trainer (in ANT+ FE-C packets) and processed.
+ At any time the App user changes the current settings or control data, the Companion App sends these to the SIMCLINE to make use of.
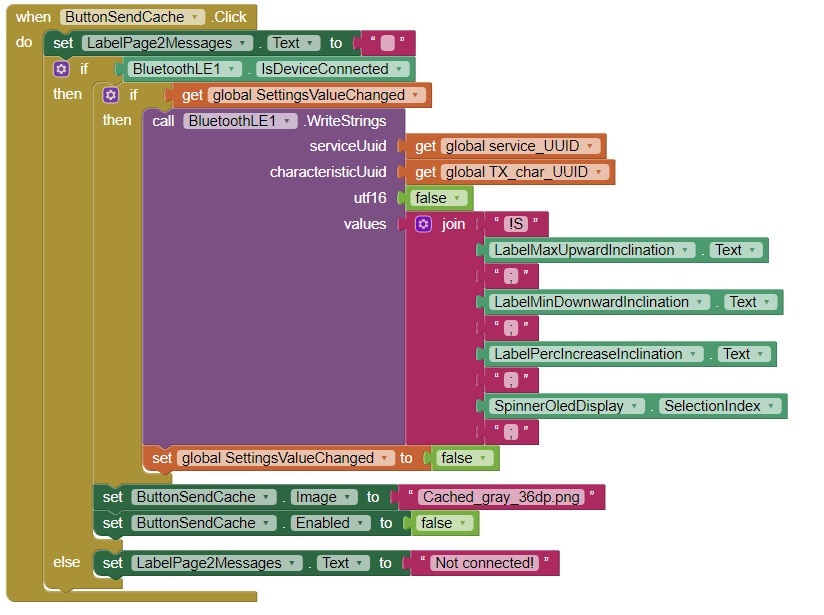
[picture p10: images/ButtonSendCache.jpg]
<br clear="left">
+ The SIMCLINE receives asynchronously settings and sets the appropriate operational variables in accordance. This determines instantly the working of the equipment.
+ The settings are persistently stored for future use.
```C++
.
void prph_bleuart_rx_callback(uint16_t conn_handle) {
  (void) conn_handle;
// Read data received over BLE Uart from Mobile Phone
  char RXpacketBuffer[20+1] = { 0 };
  bleuart.read(RXpacketBuffer, 20);
// The following routines parse and process the incoming commands
// Every RXpacket starts with a '!' otherwise corrupt/invalid
  if (RXpacketBuffer[0] != '!'){
    return; // invalid RXpacket: do not further parse and process
  }
.
.
 // New Settings values have arrived --> parse, set values and store persistently
   uint8_t iMax = 0, iMin = 0, iPerc = 0, iDispl = 0;
   sscanf(RXpacketBuffer, "!S%d;%d;%d;%d;", &iMax, &iMin, &iPerc, &iDispl);
 // set aRGVmax
   aRGVmax = map(iMax, 0, 20, 20000, 22000);
 // set aRGVmin
   aRGVmin = map(iMin, 10, 0, 19000, 20000);
 // set PercIncreaseInclination
   PercentageIncreaseValue = iPerc;
 // set OledDisplaySelection
   OledDisplaySelection = iDispl;
 // LittleFS for persistent storage of these values
 setPRSdata();
.
.
```
+ In addition to the OLED display the Companion App can serve as an enhanced screen for road grade and cycling data.
+ Until the BLE connection is disconnected, manually or by quitting the App, both devices remain connected.

# Simcline in TTS4 controlled operation<br>
In the following images is shown how the Simcline is operating when different inclination values are applied by the training software. In the present situation the Simcline is controlled by the TACX Training System (TTS4 is no longer supported by Tacx). The software is still running on my laptop and is operating in Workout Mode: <b>Slope-Time</b>. After setting the slope (in workout mode by the user) the Tacx trainer is instructed to set resistance exactly with that inclination. The Simcline polls regularly for this value with the Tacx trainer and sets the height of the front wheel axle in accordance. Notice the position and inclination with respect to the measuring tape. The measuring tape starts (zero centimeter position) at the lowest possible position of -10%. 10 Centimeter height is flat road level (0% inclination)....<br> Notice that TTS4 in this mode is <b>WhatYouSeeIsWhatYouGet</b>, the inclination that is shown on the app screen is exactly sent to the trainer for resistance setting!<br>
Please notice that today many training apps are concerned more about "<i>the optimal user experience</i>" rather than with <b>WYSIWYG</b>, with respect to the road inclination. Most apps manipulate in some way the inclination that is sent to the trainer. When it is made clear <b>HOW</b> that inclination is manipulated (like the Difficulty Setting with Zwift) one can choose to allow for that <i>optimal user experience</i> or undo the setting and go for real road feel!<br>
So when the Simcline seems not to follow the road inclination values on the training app screen, be aware that the training app is <b>NOT WYSIWYG</b>!
<br>

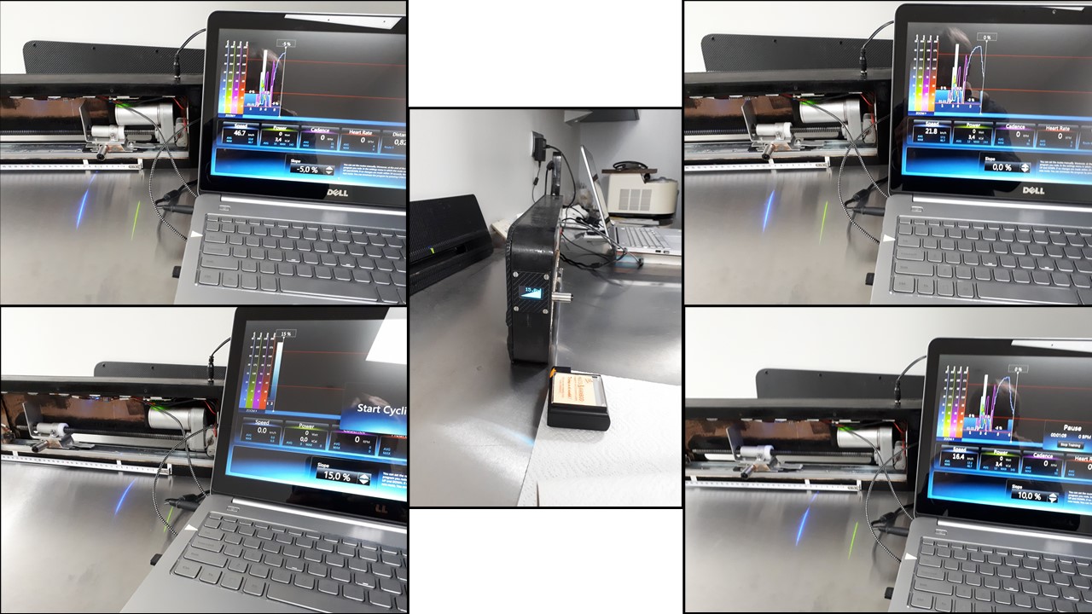
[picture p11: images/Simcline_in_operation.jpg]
Simcline at work
<br clear="left">
<br>

# [Code support for Wahoo KICKR trainers](https://github.com/Berg0162/simcline/tree/master/Wahoo%20Kickr/)<br>

# [Code support for FTMS-enabled trainers](https://github.com/Berg0162/simcline/tree/master/FTMS%20Enabled)<br>

# Mechanical Construction of SIMCLINE<br>
There are elaborated <b>Instructables</b> available with all the nitty gritty of how to create, construct and install the various parts and components of the SIMCLINE.<br> 

# SIMCLINE 1.0<br>
See: Instructables [SIMCLINE 1.0 Instructables](https://www.instructables.com/id/SIMCLINE-Simulation-of-Changing-Road-Incline-for-I/)<br clear="left">

# SIMCLINE 2.0<br>
See: Instructables [SIMCLINE 2.0 Instructables](https://www.instructables.com/SIMCLINE-20-Easy-Simulation-of-Road-Incline/)<br clear="left">

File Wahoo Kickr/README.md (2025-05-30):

# SIMCLINE Icon &nbsp; SIMCLINE for Wahoo KICKR (nRF52/ESP32)
# Simulation of Changing Road Inclination for Indoor Cycling <br>
SIMCLINE
SIMCLINE 2
The SIMCLINE physically adjusts the bike position to mimic hilly roads, climbing and descending. This allows the rider to naturally change position on the bike, engage climbing muscles, and improve pedaling technique to become a more efficient and powerful climber.<br>
Without user intervention the SIMCLINE will replicate inclines and declines depicted in (online & offline) training programs (like <b>Zwift, Rouvy, VeloReality, myWhoosh</b> and many others) that adjust accordingly the resistance of the indoor trainer.<br>
The SIMCLINE auto connects at power up with a smart Wahoo KICKR trainer and let's relive the ascents and descents from favorite rides or routes while training indoors.<br>
The physical reach is: 20% maximum incline and -10% maximum decline. However, the reach that the rider is comfortable with can be adjusted!<br>
The SIMCLINE pairs directly to the Wahoo KICKR smart trainer and with your PC/Laptop with (Zwift) training App for a connection that notifies the SIMCLINE to simulate autonomous the (change in) physical grade of the road during an indoor ride.<br>
During operation an OLED display shows the road grade in digits and in graphics.<br>
The SIMCLINE Companion App (for Android smartphones) can be paired, only when the training App is disconnected, for adjusting operational settings, like Ascent Grade Limit (between 0-20%), Descent Grade Limit (between 0-10%), Road Grade Change Factor (between 0-100%) and manual Up and Down control. Notice that the Companion App has a slightly different functionality depending of what brand of trainer (TACX or Wahoo) is connected, due to specific connectivity differences. <br clear="left"> 

# Credits to Christian B. from Canada
Christian was one of those that have a Wahoo KICKR trainer and built the SIMCLINE design for personal use. However, he could not apply the SIMCLINE code as it was! We have collaborated very closely during a teamwise journey to explore all possible scenarios to realize the SIMCLINE design and code to operate with a Wahoo KICKR trainer, in addition to a TACX trainer! Christian's expertise and effort was focussed on testing with Wahoo KICKR and figure out how (Zwift-KICKR) communication is implemented. He collected tons of valuable information that helped to find out how things work, pinpoint causes of failures and at the end to construct the present working solution. Without his valuable effort this project would never have taken place!<br>
If you need to modify your Wahoo Kickr trainer, see Christian's effort: [Free Axle for Wahoo KICKR Gen2](https://www.instructables.com/Free-Axle-for-Wahoo-Kickr-Gen2-2018/)<br>

# Man-In-The-Middle (MITM) software pattern<br>
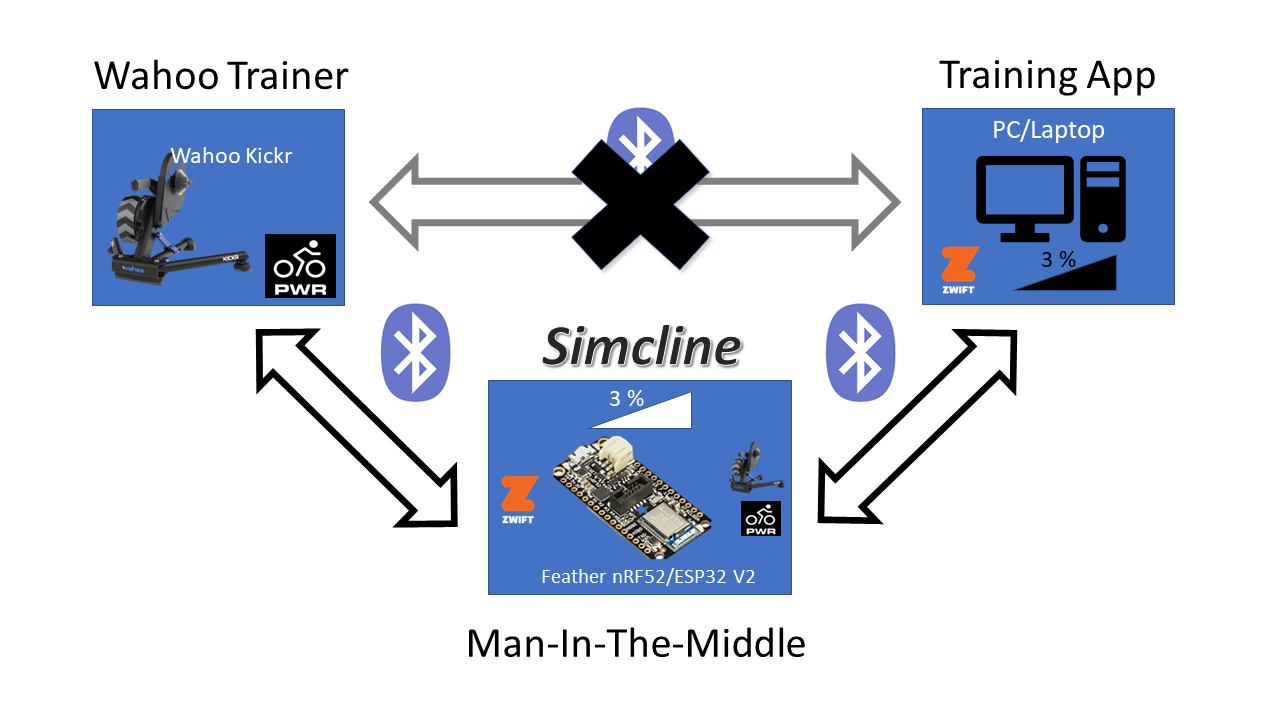
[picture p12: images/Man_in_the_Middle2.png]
Man in the Middle
<br>
TACX published in 2015 a document [TACX, FE-C and Bluetooth](https://github.com/Berg0162/simcline/blob/master/docs/How_to_FE_C_over_BLE_v1_0_0.pdf) that explains how to use the FE-C ANT+ protocol over BLE feature implemented on all(?) TACX Smart Trainers. TACX designed this feature because at that time an open standard (on BLE) for trainers was lacking. However Wahoo did not officially publish any document describing their proprietary protocol to control a Wahoo KICKR over BLE. The major training App developers were invited (by Wahoo) to design their Apps for use with Wahoo products. No doubt they had to sign a non-disclosure agreement. While TACX has been transparent, Wahoo was definitely NOT! However, the internet is a great source for information about not so transparent companies. At first the SIMCLINE was designed to successfully work with smart TACX trainers and after publication in the public domain several people applied the design to built their own. However most remarks/questions I received were about the application of a Wahoo KICKR trainer. Early in the year 2022, we decided to put a jont effort in modifying the Simcline code in such a way that it would operate with a Wahoo KICKR. After other scenarios had failed, I have chosen to apply the Man-in-the-middle software pattern, since that should work with all smart Wahoo KICKR trainers, young and relatively older!<br>

<b>Man-In-The-Middle</b> is a powerful software engineering pattern that is applied in many software designs. Unfortunately it is also known for a negative application in communication traffic: MITM is a common type of cybersecurity attack that allows attackers to eavesdrop on the communication between two targets.
We have applied the very principle: the Simcline is strategicly positioned in between the BLE communication of the Wahoo KICKR Trainer and the training App (like Zwift) running on the PC/Laptop, all communication traffic can be inspected in that MITM position, when it is passed on from one to the other, in both directions. When Zwift sends resistance information (like the road inclination) to the Wahoo KICKR, this information can be intercepted and applied to determine the up/down positioning of the Simcline. <br>

Meanwhile there is well documented (<b>FTMS</b>) FiTness Machine Service protocol to control fitness equipment over Bluetooth. According to the smart trainer recommendations guide winter 2019-2020 of [DCRainmaker](https://www.dcrainmaker.com/2019/10/the-smart-trainer-recommendations-guide-winter-2019-2020.html) the situation evolved:
> Meanwhile, for Bluetooth Smart, there’s FTMS, which is basically the same thing as FE-C when it comes to trainers. It’s not quite as widely adopted yet by trainer companies, but is by app companies. On the trainer company side only Elite, Saris, and Kinetic support it across the board. With Tacx having it on some but not all units, and Wahoo having it on no units (but all Wahoo and Tacx trainers support a <b>proprietary</b> Bluetooth Smart with all major apps anyway).<br>

A next generation of Simclines will hopefully be based on this FTMS, when all companies embrace its open standard, however, today we still have to open our box of tricks! <br>

# Choose a Development board: nRF52840 or ESP32?<br>
Until early 2023 the Simcline project (a.o.) solely worked with the <b>Feather nRF52840 Express</b> development board and the Bluefruit/Adafruit libraries. This is a very stable platform and gave reliable results during development and what's more during many indoor seasons of 5 hours per week operation! However, the MITM application and actuator control (a.k.a. Simcline) is at the capacity limits of the nRF52840 processor. 
See for a reliable and <b>proven</b> solution: [Adafruit Feather nRF52840 Express](https://learn.adafruit.com/introducing-the-adafruit-nrf52840-feather) <br>

So the question was raised why not use the <b>ESP32</b>, a series of low-cost and low-power System on a Chip (SoC) microcontrollers developed by Espressif that include Wi-Fi and Bluetooth wireless capabilities and dual-core processor? See for an introduction: [Random Nerds Tutorials](https://randomnerdtutorials.com/getting-started-with-esp32/). Particularly the multiprocessing capabilities of the dual-core processor make the ESP32 a very tempting option in this project!
To benefit of the same formfactor (fits with the Simcline 2.0 component box!), I decided to (re)produce the Simcline code with the [Adafruit Feather ESP32 V2](https://learn.adafruit.com/adafruit-esp32-feather-v2) for the <b>ESP32</b> platform. Just comparing the overal specs (on paper) of both processor platforms is not sufficient... one needs to take into account the (quality of the) available libraries as well to reach success. The 'standard' ESP32 Arduino <b>Bluedroid</b> library (for BLE support) turned out to be buggy! Fortunately [H2Zero](https://github.com/h2zero/NimBLE-Arduino) has created a more or less compatible replacement for Bluedroid, called <b>NimBLE-Arduino</b>! The application of <b>NimBLE</b> saved the porting of the software to the ESP32 platform! 
In week 9 of 2023 the ESP32 code reached a stable level and became publicly available for testing with Wahoo Kickr trainers.

# How to start?<br>
+ Install the [Arduino IDE](https://www.arduino.cc/en/Main/Software) and all the libraries on a PC/Mac.
+ If you are using an ESP32 board then also download the ESP32 NimBLE library, see [Arduino Installation NimBLE](https://github.com/h2zero/NimBLE-Arduino#arduino-installation)
+ Download all the code from [Github](https://github.com/Berg0162/simcline) and install.
<br>
Cardboard
When I started the project in 2020 I did not have any practical experience with any of the components. So I had to setup the circuitry step by step adding components and did a lot of time consuming but instructive testing first. My advice is to setup (<b>some of</b>) the electronic components first in a similar way as shown on the photo with the cardboard base. Use double sided adhesive tape but only attach it on sections that have no pcb-wiring or soldering, to avoid possible electrical interference. You will find in this Github repository all the code that controls the Simcline and the Arduino test programs (modified for this project) that focus on components separately and in conjunction. <br clear="left">

# To see is to believe!<br>
I can understand and respect that you have some reserve: Is this really working in my situation? Better test if it is working, before buying all components and start building.
In the Github repository (see above) you will find the appropriate test code named: <b>Wahoo_Client</b>, <b>Wahoo_Server</b> and <b>Wahoo_Zwift_Bridge</b>. It is coded with the only intention to check if the MITM solution is delivering in your specific situation.<br>

<b>What it does in short:</b><br>
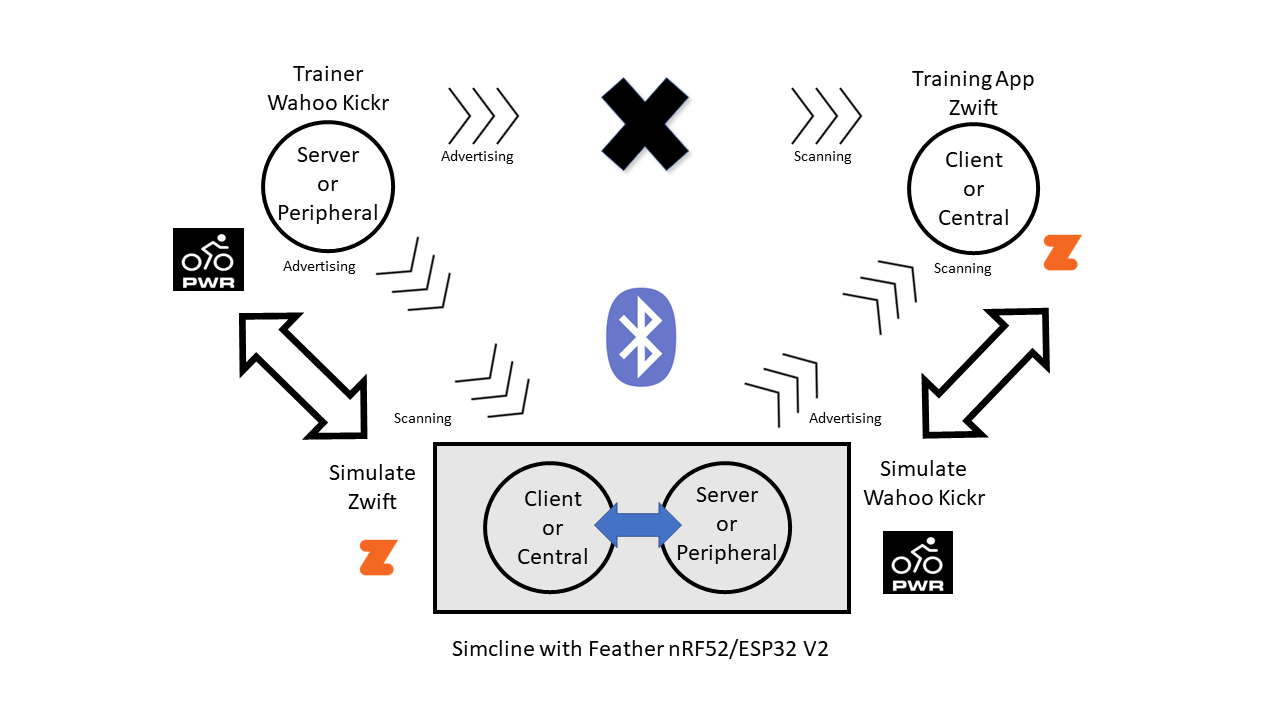
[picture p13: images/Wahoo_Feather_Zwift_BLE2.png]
Simcline in the Middle
<br>
The <b>Wahoo_Zwift_Bridge</b> code links a bike trainer (BLE Server Wahoo KICKR) and a PC/Laptop (BLE Client running Zwift) with the Feather nRF52/ESP32, like a bridge in between. The MITM bridge can pass on, control, filter and alter the interchanged trafic data! This test code is fully ignorant of the mechanical components that drive the Simcline. It simply estabishes a virtual BLE bridge and allows you to ride the bike on the Wahoo trainer and feel the resistance that comes with it, thanks to Zwift. The experience should not differ from a normal direct one-to-one connection, Zwift - Wahoo KICKR!<br>
+ The client-side scans and connects with the Wahoo relevant Cycling Power Service (<b>CPS</b>) plus the additional Wahoo proprietary CPS characteristic and collects cyling power data like Zwift would do! The code with the name: <b>Wahoo_Client</b> is doing just that one side of the "bridge"!
+ The Server-side advertises and enables connection with Cycling apps like Zwift and collects relevant resistance data, it simulates as if an active Wahoo trainer is connected to Zwift or alike! The code with the name: <b>Wahoo_Server</b> is doing just the other side of the "bridge"!
+ The <b>Wahoo_Zwift_Bridge</b> code is connecting both sides at the same time: the full-blown bridge!<br clear="left">

<b>How to make it work?</b><br>
The requirements are simple: 
+ running Zwift app or alike, 
+ working Feather nRF52840 or Adafruit ESP32 Feather V2
+ a Wahoo KICKR trainer.<br>

<b>Use the test code for reconnaissance!</b><br>
Please follow the instructions at the first part of the program code!
+ Start your reconnaissance with running <b>Wahoo_Client</b> and experience how the Feather is controlling the resistance of your Wahoo trainer. 
+ Next step is running <b>Wahoo_Server</b>, pairing with Zwift and then notice how your avatar is moving effortless in the Zwift world controlled by the Feather.<br>

<i>The 3 test programs (Client, Server and Bridge) are <b>ONLY</b> utilizing Serial Monitor to show what is happening!</i><br>
Please write down the MAC or Device Addresses of a) your Wahoo trainer and b) your Desktop/Laptop with Zwift. These are presented in the Serial Monitor log file when running the Client, Server and Bridge test code.<br>

<b>Now it is time to test the bridge!</b><br>
The <b>Wahoo_Zwift_Bridge</b> code needs these "hardware" addresses to unmistakingly establish a BLE connection with the right device. I know it can be implemented differently but this is to avoid unwanted BLE connection(s) with an additional power meter, another fitness device or a second computer/laptop, etcetera. 
```C++
.
// -----------------------------------------------------------------
// Your hardware MAC/DEVICE ADDRESSES
// Laptop/Desktop Device Address that runs Zwift: [00:01:02:03:04:05]
// Little Endian: in reversed order !!!!
#define LAPTOPADDRESS {0x05,0x04,0x03,0x02,0x01,0x00}
// Trainer Wahoo KICKR Device Address [00:01:02:03:04:05]
// Little Endian: in reversed order !!!!
#define TRAINERADDRESS {0x05,0x04,0x03,0x02,0x01,0x00}
// -----------------------------------------------------------------
.
```
The two precise device addresses are critical to assure a reliable test! You have to insert the values in the program code!<br> 

1) First insert in the <b>Wahoo_Zwift_Bridge</b> code the two precise BLE MAC Addresses it has to connect with
2) Upload and Run this code on the Feather nRF52840 Express or Adafruit ESP32 Feather V2
2) Start the Serial Monitor to catch debugging info
3) Start/Power-On the Wahoo trainer  
4) Feather and Trainer will pair as reported on the Serial Monitor
5) Start Zwift on your computer or tablet
6) Search on Zwift pairing screen "<b>Power</b>" for the Feather a.k.a. "<b>SIM32</b>" or "<b>SIM52</b>"
7) Pair <b>Power</b> and <b>Controllable</b> with "<b>SIM32</b>" or "<b>SIM52</b>"
8) Notice Wahoo does NOT support Speed nor Cadence, optionally pair with alternative
9) After successful pairing start the default Zwift ride or any ride you wish
10) Make Serial Monitor visible on top of the Zwift window 
11) Hop on the bike and make it happen..
12) Inspect the info presented by Serial Monitor for the Zwift road inclination values.....
<br clear="left">

# Dual Processor use with ESP32
One of the advantages of the ESP32 platform is the fact that the ESP32 WROOM processor has two cores. This makes it possible to precisely balance the load of a program over 2 processor cores. <br>
Arduino IDE 2.0 Tools Menu
With the Simcline this is particular usefull for the motor control of the actuator. During operation Zwift sends from time to time new settings, and one of these is the grade value (road inclination in degrees). The program translates the grade to a level that should be reached by the actuator to simulate exactly the road grade that was received from Zwift. However, the actuator can only be switched to <b>move up</b>, <b>move down</b> or <b>stop</b>. After  having set the actuator to move (up or down), the program has to check continuously if the actuator has reached the desired level by reading its position with the help of the Time-Of-Flight sensor and act accordingly. Meanwhile the trainer sends your cycling data and the Zwift app has to confirm the receipt of these data. The data sent by Zwift has also to be tranferred to the trainer and also the trainer has to confirm the receipt. Being a MITM means handling a lot of BLE traffic and it does not allow for mistakes!
The load of the Simcline program itself, the BLE handling and the critical control of the actuator is balanced over 2 processor cores on the ESP32 platform.
The following code snippets show how this is achieved for controlling the actuator motor. To avoid conflicts during variable updates (i.c. TargetPosition) a Binary Semaphore scheme is applied to protect <b>task shared variables</b> during an update.<br clear="left">

At the start the major players are defined
```C++
.
// ----------------------xControlUpDownMovement task definitions ------------------
SemaphoreHandle_t xSemaphore = NULL;
TaskHandle_t ControlTaskHandle = NULL;
// Set Arduino IDE Tools Menu --> Events Run On: "Core 1"
// Set Arduino IDE Tools Menu --> Arduino Runs On: "Core 1"
// Run xControlUpDownMovement on "Core 0"
const BaseType_t xControlCoreID = 0;
void xControlUpDownMovement(void* arg); 
// --------------------------------------------------------------------------------
.
```
In the setup() routine the variables are instantiated (after checking the mechanics of the motor function) and the <b>xControlUpDownMovement</b> task is pinned to processor <b>core 0</b>, with a priority of 10. Most of the Simcline program and Events are running on <b>core 1</b>.
```C++
.
  } else {
    ShowOnOledLarge("Testing", "Functions", "Done!", 500);
    // Is working properly --> Start Motor Control Task
    xSemaphore = xSemaphoreCreateBinary();
    xTaskCreatePinnedToCore(xControlUpDownMovement, "xControlUpDownMovement", 4096, NULL, 10, &ControlTaskHandle, xControlCoreID);
    xSemaphoreGive(xSemaphore);
    DEBUG_PRINTLN("Motor Control Task Created and Active!");        
    IsBasicMotorFunctions = true;
    DEBUG_PRINTLN("Simcline Basic Motor Funtions are working!!");
    // Put Simcline in neutral: flat road position
#ifdef EMA_ALPHA
    // Init EMA filter at first call with flat road position as reference
    TargetPosition = EMA_TargetPositionFilter(TargetPosition); 
#endif
    SetNewActuatorPosition();
  }
.
```
Whenever new values for the road grade are received these are translated to a physical actuator position (level above ground) and the <b>TargetPosition</b> is set during Semaphore protection. When the new position has been set, the protection is cancelled, and the motor control task can access the new setting.
```C++
.
void SetNewActuatorPosition(void) {
  // Handle mechanical movement i.e. wheel position in accordance with Road Inclination
  // Map RawgradeValue ranging from 0 to 40.000 on the
  // TargetPosition (between MINPOSITION and MAXPOSITION) of the Lifter
  // Notice 22000 is equivalent to +20% incline and 19000 to -10% incline
  RawgradeValue = constrain(RawgradeValue, RGVMIN, RGVMAX); // Keep values within the safe range
  TargetPosition = map(RawgradeValue, RGVMIN, RGVMAX, MAXPOSITION, MINPOSITION);
  // EMA filter for smoothing quickly fluctuating Target Position values see: Zwift Titan Grove
#ifdef EMA_ALPHA
  TargetPosition = EMA_TargetPositionFilter(TargetPosition);
#endif
  if(IsBasicMotorFunctions) {  
    xSemaphoreTake(xSemaphore, portMAX_DELAY); 
    lift.SetTargetPosition(TargetPosition);
    xSemaphoreGive(xSemaphore);
#ifdef MOVEMENTDEBUG
    DEBUG_PRINTF("RawgradeValue: %05d Grade percent: %03.1f%% ", RawgradeValue, gradePercentValue);
    DEBUG_PRINTF("TargetPosition: %03d\n", TargetPosition, DEC);
#endif
  }  
}
.
```
The motor control task regularly checks how far off the actuator position is from its target position and if it should be braked yet. However, it happens all the time that the road grade changed from upward to flat or to downward. The actuator should follow these changes and therefore the motor is switched many times to brake or to reverse its movement. When the motor control task is accessing the relevant variables the semaphore is protecting these against updates!
```C++
void xControlUpDownMovement(void *arg) {
  // Check "continuously" the Actuator Position and move Motor Up/Down until target position is reached
  int OnOffsetAction = 0;
  const TickType_t xDelay = 110 / portTICK_PERIOD_MS; // Block for 110ms < 10Hz sample rate of VL6180X
  while(1) {
    if(xSemaphoreTake(xSemaphore, portMAX_DELAY)) {
        // BLE channels can interrupt and consequently target position changes on-the-fly !!
        // We do not want changes in TargetPosition during one of the following actions!!!
        OnOffsetAction = lift.GetOffsetPosition(); // calculate offset to target and determine action
        switch (OnOffsetAction)
            {
              case 0 :
                lift.brakeActuator();
                #ifdef MOVEMENTDEBUG
                DEBUG_PRINTLN(F(" -> Brake"));
                #endif
                break;
              case 1 :
                lift.moveActuatorUp();
                #ifdef MOVEMENTDEBUG
                DEBUG_PRINTLN(F(" -> Upward"));
                #endif
                break;
              case 2 :
                lift.moveActuatorDown();
                #ifdef MOVEMENTDEBUG
                DEBUG_PRINTLN(F(" -> Downward"));
                #endif
                break;
              case 3 :
                // Timeout --> OffsetPosition is undetermined --> do nothing and brake
                lift.brakeActuator();
                #ifdef MOVEMENTDEBUG
                DEBUG_PRINTLN(F(" -> Timeout"));
                #endif
                break;
            } // switch 
        xSemaphoreGive(xSemaphore);    
    }      
    vTaskDelay(xDelay);
  } // while
} // end
```

# Overview of Wahoo Simcline nRF52 Code Flow and Snippets<br>
+ Include headers of libraries and declare classes
```C++
.
#include <bluefruit.h>
// Compile toggle that determines Serial Monitor is switched ON (1) or OFF (0)
#define Serial_Monitor 1
// Libraries for use of I2C devices (Oled and VL6180X distance sensor)
#include <SPI.h>
#include <Wire.h>
// Necessary libraries for use of Oled display(s)
#include <Adafruit_GFX.h>
#include <Adafruit_SSD1306.h>
// Additional splash screen bitmap and icon(s) for Oled
#include "Adafruit_SSD1306_Icons.h" // needs to be in directory of main code
// Declarations for an SSD1306 128x64 display connected to I2C (SDA, SCL pins)
#define SCREEN_WIDTH 128            // SSD1306-OLED display width, in pixels
#define SCREEN_HEIGHT 64            // SSD1306-OLED display height, in pixels
#define OLED_RESET -1               // No reset pin on this OLED display
#define OLED_I2C_ADDRESS 0x3C       // I2C Address of OLED display
// Declare the display
Adafruit_SSD1306 display(SCREEN_WIDTH, SCREEN_HEIGHT, &Wire, OLED_RESET);
#include <avr/dtostrf.h>
.
```
+ Declare crucial BLE services, variables and charateristics 
```C++
.
/* Cycling Power Service
 * CP Service: 0x1818  
 * CP Characteristic: 0x2A63 (Measurement)
 * CP Characteristic: 0x2A65 (Feature)
 * CP Characteristic: 0x2A5D (Location) NOT supported in Wahoo legacy trainers
 * CP Characteristic: 0x2A66 (CYCLING_POWER_CONTROL_POINT)
 */
 // --------------------------------------------------------------------------------------------------------------------------------------------
BLEService        server_cps = BLEService(UUID16_SVC_CYCLING_POWER);
// Define how Server CPS is advertised
const uint16_t Server_appearance = 0x0480;  // 1152 -> Cycling
BLECharacteristic server_cpmc = BLECharacteristic(UUID16_CHR_CYCLING_POWER_MEASUREMENT);
BLECharacteristic server_cpfc = BLECharacteristic(UUID16_CHR_CYCLING_POWER_FEATURE);
BLECharacteristic server_cplc = BLECharacteristic(UUID16_CHR_SENSOR_LOCATION);
BLECharacteristic server_cpcp = BLECharacteristic(UUID16_CHR_CYCLING_POWER_CONTROL_POINT); // Indicate, write

// Hidden Wahoo Trainer characteristic to the Cycling Power Service !
// Unknown Characteristic is 128 bit:            A0 26 E0 05 - 0A 7D - 4A B3 - 97 FA - F1 50 0F 9F EB 8B
// Declare in Reversed order !!!
uint8_t CYCLING_POWER_WAHOO_TRAINER_Uuid[16] = {0x8B, 0xEB, 0x9F, 0x0F, 0x50, 0xF1, 0xFA, 0x97, 0xB3, 0x4A, 0x7D, 0x0A, 0x05, 0xE0, 0x26, 0xA0};
BLECharacteristic server_cpwt = BLECharacteristic(CYCLING_POWER_WAHOO_TRAINER_Uuid);

// Server helper class instance for Device Information Service
BLEDis bledis;

//-----------------------------------------------------------------------------------------------------------------------------------------------
BLEClientService        client_cps(UUID16_SVC_CYCLING_POWER);
BLEClientCharacteristic client_cpmc(UUID16_CHR_CYCLING_POWER_MEASUREMENT);
BLEClientCharacteristic client_cpfc(UUID16_CHR_CYCLING_POWER_FEATURE);
uint32_t client_cpfcDef = 0;
BLEClientCharacteristic client_cplc(UUID16_CHR_SENSOR_LOCATION);
uint16_t client_cplc_loc_value = 0;
BLEClientCharacteristic client_cpcp(UUID16_CHR_CYCLING_POWER_CONTROL_POINT); // Indicate, write
BLEClientCharacteristic client_cpwt(CYCLING_POWER_WAHOO_TRAINER_Uuid);
.
```
```C++
.
// CPS Wahoo Trainer Operation Codes in Decimal
const uint8_t unlock                     = 32;
const uint8_t setResistanceMode          = 64;
const uint8_t setStandardMode            = 65;
const uint8_t setErgMode                 = 66;
const uint8_t setSimMode                 = 67;
const uint8_t setSimCRR                  = 68;
const uint8_t setSimWindResistance       = 69;
const uint8_t setSimGrade                = 70;
const uint8_t setSimWindSpeed            = 71;
const uint8_t setWheelCircumference      = 72;
const uint8_t UnlockCommandBuf[3]        = {unlock, 0xEE, 0xFC}; // Unlock codes
.
```
```C++
.
#define SERVICE_DEVICE_INFORMATION                  0x180A
#define CHARACTERISTIC_MANUFACTURER_NAME_STRING     0x2A29
#define CHARACTERISTIC_MODEL_NUMBER_STRING          0x2A24
#define CHARACTERISTIC_SERIAL_NUMBER_STRING         0x2A25

// Client Service Device Information
BLEClientService        client_diss(SERVICE_DEVICE_INFORMATION);
BLEClientCharacteristic client_disma(CHARACTERISTIC_MANUFACTURER_NAME_STRING);
BLEClientCharacteristic client_dismo(CHARACTERISTIC_MODEL_NUMBER_STRING);
BLEClientCharacteristic client_dissn(CHARACTERISTIC_SERIAL_NUMBER_STRING);
.
```
```C++
.
/* ------------------------------------------------------------------------------------------------
 * Warning I/O Pins have identical position but different naming depending on the processor board
 * I/O Pin declarations for connection to Motor driver board MDD3A
*/
#if defined(ARDUINO_NRF52840_FEATHER) 
  #define actuatorOutPin1 A0   // --> A0/P0.02 connected to pin M1A of the MDD3A Motor Driver board
  #define actuatorOutPin2 A1   // --> A1/P0.03 connected to pin M1B of the MDD3A Motor Driver board
#endif
#if defined(ARDUINO_NRF52832_FEATHER) 
  #define actuatorOutPin1 2    // --> A0/P0.02 connected to pin M1A of the MDD3A Motor Driver board
  #define actuatorOutPin2 3    // --> A1/P0.03 connected to pin M1B of the MDD3A Motor Driver board
#endif
.
// Declaration of Function prototypes
int16_t EMA_TargetPositionFilter(int16_t current_value); // EMA filter function for smoothing Target Position values
void ShowIconsOnTopBar(void);
void ShowOnOledLarge(const char* Line1, const char* Line2, const char* Line3, uint16_t Pause);
void ShowSlopeTriangleOnOled(void);

void SetNewRawGradeValue(float RoadGrade);
void SetManualGradePercentValue(void);
void SetNewActuatorPosition(void);
void ControlUpDownMovement(void);

bool getPRSdata(void);
void setPRSdata(void);

void StartAdvBLEuart(void);
void prph_bleuart_rx_callback(uint16_t conn_handle);

void Setup_Client_CPS(void);
void Client_Start_Scanning(void);
void client_scan_callback(ble_gap_evt_adv_report_t* report);
void Client_Enable_Notify_Indicate(void);
void Client_connect_callback(uint16_t conn_handle);
void Get_client_Diss(uint16_t conn_handle);
void Client_disconnect_callback(uint16_t conn_handle, uint8_t reason);
void client_cpcp_indicate_callback(BLEClientCharacteristic* chr, uint8_t* data, uint16_t len);
void client_cpmc_notify_callback(BLEClientCharacteristic* chr, uint8_t* data, uint16_t len);
void client_cpwt_indicate_callback(BLEClientCharacteristic* chr, uint8_t* data, uint16_t len);

void Setup_Server_CPS(void);
void Start_Server_Advertising(void);
void server_cpwt_callback(uint16_t conn_hdl, BLECharacteristic* chr, uint8_t* data, uint16_t len);
void server_cpcp_callback(uint16_t conn_hdl, BLECharacteristic* chr, uint8_t* data, uint16_t len);
void Periph_adv_stop_callback(void);
void Periph_connect_callback(uint16_t conn_handle); 
void Periph_disconnect_callback(uint16_t conn_handle, uint8_t reason);
void server_cccd_callback(uint16_t conn_handle, BLECharacteristic* chr, uint16_t cccd_value);
// End Function Definitions
```
<b>Begin of the Arduino Setup() Function</b><br>
+ Get or set (first time only) the values of relevant and crucial variables to persistence, whith the Companion App the user can set these on the fly!
+ Start the show for the SSD1306 Oled display.
+ Initialize Lifter Class data, variables, test and set to work!
```C++
.
  //Show Name and SW version on Oled
  ShowOnOledLarge("SIMCLINE", "Wahoo", "3.4.4", 500);
  // Initialize Lifter Class data, variables, test and set to work !
  lift.Init(actuatorOutPin1, actuatorOutPin2, MINPOSITION, MAXPOSITION, BANDWIDTH);
.
```
```C++
.
  // Test Actuator and VL8106X for proper functioning
  ShowOnOledLarge("Testing", "Up & Down", "Functions", 100);
  if (!lift.TestBasicMotorFunctions()) {
    ShowOnOledLarge("Testing", "Functions", "Failed!", 500);
    IsBasicMotorFunctions = false; // Not working properly
#if Serial_Monitor  
    Serial.println("Basic Motor Funtions are NOT working!!");
#endif
    }
  else {
    ShowOnOledLarge("Testing", "Functions", "Done!", 500);
    // Is working properly
    IsBasicMotorFunctions = true;
#if Serial_Monitor  
    Serial.println("Basic Motor Funtions are working!!");
#endif
    // Put Simcline in neutral: flat road position
    // Init EMA filter at first call with flat road position as reference
    TargetPosition = EMA_TargetPositionFilter(TargetPosition); 
    SetNewActuatorPosition();
    ControlUpDownMovement();
  }
.    
```
+ Initialize BLE with maximum connections as Peripheral = 1, Central = 1 and start...
```C++
.
  // begin (Peripheral = 1, Central = 1)
  Bluefruit.begin(1, 1);
  // Set the device name (keep it short!) 
#if Serial_Monitor
  Serial.println("Setting Device Name to 'SIM52'");
#endif
  // Supported tx_power values depending on mcu:
  // - nRF52832: -40dBm, -20dBm, -16dBm, -12dBm, -8dBm, -4dBm, 0dBm, +3dBm and +4dBm.
  // - nRF52840: -40dBm, -20dBm, -16dBm, -12dBm, -8dBm, -4dBm, 0dBm, +2dBm, +3dBm, +4dBm, +5dBm, +6dBm, +7dBm and +8dBm.
  Bluefruit.setTxPower(4); // See above for supported values: +4dBm
  Bluefruit.setName("SIM52");

  Setup_Client_CPS();
  Client_Start_Scanning();
  while (Bluefruit.Scanner.isRunning()) { // do nothing else but scanning....
  }
#if Serial_Monitor 
  Serial.println("Scanning for Wahoo Cycle Power Service is stopped!");
#endif  
  TimeInterval = millis() + TIME_SPAN; // ADD just enough delay
  // wait enough time or go on when client is connected and set!
  while ( (TimeInterval > millis()) || (!Trainer.IsConnected) ) {
    }

  // Setup the Server Cycle Power Service
  // BLEService and BLECharacteristic classes initialized
  Setup_Server_CPS();
  Start_Server_Advertising();
  
  while (Bluefruit.Advertising.isRunning()) { // ONLY advertise!
  }
#if Serial_Monitor 
  Serial.println("Wahoo Simulated Advertising stopped! Paired to Zwift?");
#endif  
  TimeInterval = millis() + TIME_SPAN; // ADD just enough DELAY
  // wait enough time or go on when server is connected and set!
  while ( (TimeInterval > millis()) || (!Laptop.IsConnected) ) { 
    }
  // Only now enable Client (Wahoo) data streams...
  Client_Enable_Notify_Indicate(); 
#if Serial_Monitor   
  Serial.println("Up and running!");
#endif
  // Initialize BLE Uart functionality for connecting to smartphone No advertising!!
  bleuart.begin();
  // End Setup
.
```
+ Actuator movement is controlled in this function
```C++
.
void ControlUpDownMovement(void) // Move fully controlled to the right position
{
  // Check Position and move Up/Down until target position is reached, 
  // BLE channels can interrupt and change target position on-the-fly !!
 
  if (!IsBasicMotorFunctions) { return; } // do nothing that can damage construction!!
  int OnOffsetAction = 0;
  InControlUpDownMovementLoop = true;
do {
  OnOffsetAction = lift.GetOffsetPosition(); // calculate offset to target and determine action
  switch (OnOffsetAction)
  {
    case 0 :
        lift.brakeActuator();
#if Serial_Monitor_Movement
      Serial.println(F(" -> Brake"));
#endif
      break;
    case 1 :
      lift.moveActuatorUp();
#if Serial_Monitor_Movement
      Serial.println(F(" -> Upward"));
#endif
      break;
    case 2 :
      lift.moveActuatorDown();
#if Serial_Monitor_Movement
      Serial.println(F(" -> Downward"));
#endif
      break;
    case 3 :
      // Timeout --> OffsetPosition is undetermined --> do nothing and brake
      lift.brakeActuator();
#if Serial_Monitor_Movement
      Serial.println(F(" -> Timeout"));
#endif
      break;
  }
} while ( (OnOffsetAction == 1) || (OnOffsetAction == 2) ); // Run the loop until target position is reached!
  InControlUpDownMovementLoop = false;
} // end 
.    
```
+ Road inclination data are extracted from the Server CPWT Cycling Power Wahoo Trainer data field
```C++
.
void server_cpwt_callback(uint16_t conn_hdl, BLECharacteristic* chr, uint8_t* data, uint16_t len)
{    
  // Server CPWT Cycling Power Wahoo Trainer data field
  // Transfer CPWT data from the Server (Zwift) to the Client (Wahoo)
  client_cpwt.write_resp(data, len); // Just pass on and process later!
  // Process to extract critical data values
  uint8_t cpwtDataLen = (uint8_t)len;    // Get the actual length of data bytes and type cast to (uint8_t)
  uint8_t cpwtData[cpwtDataLen];
  memset(cpwtData, 0, cpwtDataLen); // set to zero
  // Display the raw request packet actual length
#if Serial_Monitor
  Serial.printf("Server CPWT Data [Len: %d] [Data:  ", len);
#endif
  // Transfer the contents of data to cpwtData
  for (int i = 0; i < cpwtDataLen; i++) {
    if ( i <= sizeof(cpwtData)) {
      cpwtData[i] = *data++;
#if Serial_Monitor
      // Display the raw request packet byte by byte in HEX
      Serial.printf("%02X ", cpwtData[i], HEX);
#endif
    }
  }
.
.
  if (cpwtData[0] == setSimGrade) {
    uint16_t gr = ( cpwtData[1] + (cpwtData[2]*256) ); // This works perfect !!!
    float SimGrade = 100 * float( ((gr * 2.0 / 65535) - 1.0) ); // Percentage of road grade --> range: between +1 and -1 (!)
    SetNewRawGradeValue(SimGrade);
    SetNewActuatorPosition();
    ShowSlopeTriangleOnOled();
  }
  // Check position with the settings
  if (!InControlUpDownMovementLoop) {
    ControlUpDownMovement();
  } 
} // end
.    
```
+ The callback functions are dominating completely
```C++
.
void loop()
{ // Do not use ... !!!
  // -------------------------------------------------------
  // The callback/interrupt functions are dominating completely the
  // processing and loop() is never ever (!) called,
  // since there is a constant stream of BLE packets, handled with
  // high priority interrupts that are coming in!
  // -------------------------------------------------------
 }
// END of program
.
```

# SIMCLINE Companion App<br>
Companion App<br clear="left">
After the project was more or less accomplished and running, practical experience was gathered during many months. It became clear to me that a Companion App with some basic features would be very welcome.<br> You need some easy possibility to change settings that in the beginning were supposed to be set at compile time only. Insights change with time! Reprogramming the Arduino code on the Feather over USB becomes cumbersome when the SIMCLINE has to be dismantled every time! Therefore it was decided to develop a Companion App that would allow at minimal a feature for changing settings.<br clear="left">
After some exploring of the field (I had no experience with App development), the outcome was to build one (for Android) in the accessible environment of [MIT App Inventor 2](https://appinventor.mit.edu).<br>
+ Download the <b>MIT App Inventor</b> SIMCLINE Companion App code with extension *file*<b>.aia</b>
+ [Visit at AppInventor](https://appinventor.mit.edu), You can get started by clicking the orange "Create Apps!" button from any page on the website.
+ Get started and upload the SIMCLINE Companion App code.
+ Or upload the SIMCLINE Companion App <b>APK</b> to your Android device directly and install the APK. Android will call this a security vulnerability!

# Flow and Some Code Snippets<br>
+ The Simcline Companion app is differently functioning with this implementation of the Simcline Wahoo code... First of all and most important the "Bridge-Function" is a very heavy burden on the processing capacity of the Feather nRF52. This simply does NOT (!) allow the smartphone to be connected over BLE at the same time the Laptop/Desktop (with Zwift) is connected, as is the case when you have a TACX trainer connected!
+ After startup of the Simcline is established and it has paired with trainer and laptop (with Zwift), you have to disconnect (unpair) first the Simcline (a.k.a. Sim Wahoo) on the Zwift pairing screen. Only then it starts (BLE) advertising for the smartphone to connect! The Companion App (on your smartphone) establishes a connection over BLE with the Nordic UART service (a.k.a. BLEUART) for exchange of information. A simple dedicated protocol was implemented that allows for bidirectional exchange of short strings (<= 20 bytes) containing diagnostic messages or cyling variables.<br>
+ At first the SIMCLINE sends the latest (persistent) settings data to allow the App user to assess the current values.
+ From this moment on the App user can change the current settings or control data, the Companion App sends these to the SIMCLINE to make use of.
+ The SIMCLINE receives asynchronously settings and sets the appropriate operational variables in accordance. This determines only at a later stage the working of the equipment!
+ The settings are persistently stored for future use.
+ The SIMCLINE is <b>NOT</b> capable of sending on-the-fly cyling data (like Speed, Power, Cadence or Grade), however, other functionality like manual movement control is available.
+ After you have disconnected the Companion app, you can renew a BLE connection (pair) with the Laptop/Desktop (with Zwift) and continue or start riding... New settings will then be active!
Companion App<br clear="left">
```C++
.
void prph_bleuart_rx_callback(uint16_t conn_handle) {
  (void) conn_handle;
// Read data received over BLE Uart from Mobile Phone
  char RXpacketBuffer[20+1] = { 0 };
  bleuart.read(RXpacketBuffer, 20);
// The following routines parse and process the incoming commands
// Every RXpacket starts with a '!' otherwise corrupt/invalid
  if (RXpacketBuffer[0] != '!'){
    return; // invalid RXpacket: do not further parse and process
  }
.
.
 // New Settings values have arrived --> parse, set values and store persistently
   uint8_t iMax = 0, iMin = 0, iPerc = 0, iDispl = 0;
   sscanf(RXpacketBuffer, "!S%d;%d;%d;%d;", &iMax, &iMin, &iPerc, &iDispl);
 // set aRGVmax
   aRGVmax = map(iMax, 0, 20, 20000, 22000);
 // set aRGVmin
   aRGVmin = map(iMin, 10, 0, 19000, 20000);
 // set PercIncreaseInclination
   PercentageIncreaseValue = iPerc;
 // set OledDisplaySelection
   OledDisplaySelection = iDispl;
 // LittleFS for persistent storage of these values
 setPRSdata();
.
.
```

# Simcline in TTS4 controlled operation<br>
In the following images is shown how the Simcline is operating when different inclination values are applied by the training software. In the present situation the Simcline is controlled by the TACX Training System (TTS4 is no longer supported by Tacx). The software is still running on my laptop and is operating in Workout Mode: <b>Slope-Time</b>. After setting the slope (in workout mode by the user) the Tacx trainer is instructed to set resistance exactly with that inclination. The Simcline polls regularly for this value with the Tacx trainer and sets the height of the front wheel axle in accordance. Notice the position and inclination with respect to the measuring tape. The measuring tape starts (zero centimeter position) at the lowest possible position of -10%. 10 Centimeter height is flat road level (0% inclination)....<br> Notice that TTS4 in this mode is <b>WhatYouSeeIsWhatYouGet</b>, the inclination that is shown on the app screen is exactly sent to the trainer for resistance setting!<br>
Please notice that today many training apps are concerned more about "<i>the optimal user experience</i>" rather than with <b>WYSIWYG</b>, with respect to the road inclination. Most apps manipulate in some way the inclination that is sent to the trainer. When it is made clear <b>HOW</b> that inclination is manipulated (like the Difficulty Setting with Zwift) one can choose to allow for that <i>optimal user experience</i> or undo the setting and go for real road feel!<br>
So when the Simcline seems not to follow the road inclination values on the training app screen, be aware that the training app is <b>NOT WYSIWYG</b>!
<br>

Simcline at work<br clear="left">
<br>

# Question: My Wahoo KICKR is variably successful in connecting with the Simcline 2.0 (with ESP32 board) and Zwift
+ <b>Answer</b>: In most cases this behavior can be attributed to not following the critical sequence for starting and connecting, Trainer, Simcline and Zwift.<br>

0) The Start or Initial situation of <b>ALL</b> parties involved is: Laptop/Zwift, Simcline and Wahoo KICKR are Powered <b>OFF</b>!
1) Power-ON the Wahoo KICKR --> KICKR needs some time (4 seconds?) to settle and start advertising!
2) Power-ON or Reset Simcline (ESP32 board) --> Simcline needs some time to start, test motor functions and start scanning for Wahoo trainer!
3) Wait for Simcline and Wahoo KICKR to connect! 9 Out of 10 times this is immediately successful. If this is <b>NOT</b> the case then Reset Simcline first and wait again for a Simcline-Wahoo connection! If this is <b>NOT</b> successful: go back to "Start" after <b>ALL</b> components have been Powered <b>OFF</b> first.
4) Laptop/Zwift Power-ON --> <b>ONLY</b> when Simcline and Wahoo KICKR have been connected successfully!
5) Wait and wait for the Zwift pairing window to pop-up
6) Click orange POWER SOURCE button and select in the list with devices: ESP32#### (Simcline) --> Close
7) Click orange RESISTANCE button and select in the list with devices: ESP32#### (Simcline) --> Close
8) Click orange CADENCE button and select in the list with devices: ESP32#### (Simcline) --> Close (NB <b>NOT</b> all legacy Wahoo trainers support Cadence!!)
9) Click orange HEART RATE button and/or CONTROLS buttons and select in the list with devices: your choice --> Close
10) Click orange OK! button, when all the selected devices are conforming your choices and are indicated as <b>CONNECTED</b>!<br>

# [Code support for smart TACX trainers](https://github.com/Berg0162/simcline/edit/master/Tacx%20Smart/)<br>

# Mechanical Construction of SIMCLINE<br>
There are elaborated <b>Instructables</b> available with all the nitty gritty of how to create, construct and install the various parts and components of the SIMCLINE.<br> 

# SIMCLINE 1.0<br>
See: Instructables [SIMCLINE 1.0 Instructables](https://www.instructables.com/id/SIMCLINE-Simulation-of-Changing-Road-Incline-for-I/)<br clear="left">

# SIMCLINE 2.0<br>
See: Instructables [SIMCLINE 2.0 Instructables](https://www.instructables.com/SIMCLINE-20-Easy-Simulation-of-Road-Incline/)<br clear="left">

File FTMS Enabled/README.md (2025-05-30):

# The ESP32-code in the FTMS-Enabled folder of 'simcline' is Deprecated and NO Longer Maintained!

# After ESP32 NimBLE-Arduino version 2.x<br>
As of early January 2025 NimBLE-Arduino version 2.x was released and turned out to be **disruptive** for all then existing ESP32-code in the repository. It took quite some effort to make the **simcline** repository sections with ESP-code accommodate version 2.x. As a consequence, a completely new `Simcline-V2` ESP32-repository was created with **redesigned** and **improved** ESP32-code for **FTMS supporting trainers**.<br>
+ **Option #1 for ESP32 boards**<br>
Keep NimBLE-Arduio version 1.4.3 installed in your Arduino IDE when you want to use the **deprecated** ESP32-code in the **FTMS-Enabled** folder of the **simcline** repository!
Notice: Version 1.4.3 stll works fine with the deprecated `FTMS-enabled` ESP32-code in this part of the repository! **However, it is NO LONGER maintained**<br>
+ **Option #2 for ESP32 boards**<br>
`Simcline-V2` ESP32-repository has been published to supersede the deprecated ESP32-code here, checkout: [Simcline-V2](https://github.com/Berg0162/Simcline-V2)<br>

# SIMCLINE Icon &nbsp; SIMCLINE for FTMS enabled Trainers
# Simulation of Changing Road Inclination for Indoor Cycling<br>

SIMCLINE
SIMCLINE 2
The SIMCLINE physically adjusts the bike position to mimic hilly roads, climbing and descending. This allows the rider to naturally change position on the bike, engage climbing muscles, and improve pedaling technique to become a more efficient and powerful climber.<br>
Without user intervention the SIMCLINE will replicate inclines and declines depicted in (online & offline) training programs (like <b>Zwift, Rouvy, VeloReality, myWhoosh</b> and many others) that adjust accordingly the resistance of the indoor trainer.<br>
The SIMCLINE auto connects at power up with a FTMS enabled smart trainer and let's relive the ascents and descents from favorite rides or routes while training indoors.<br>
The physical reach is: 20% maximum incline and -10% maximum decline. However, the reach that the rider is comfortable with can be adjusted!<br>
The SIMCLINE pairs directly to the FTMS enabled trainer and with your PC/Laptop/Tablet with (Zwift) training App for a connection that notifies the SIMCLINE to simulate autonomous the (change in) physical grade of the road during an indoor ride.<br>
During operation an OLED display shows the road grade in digits and in graphics.<br>
The SIMCLINE Companion App (for Android smartphones) can be paired, only when the training App is disconnected, for adjusting operational settings, like Ascent Grade Limit (between 0-20%), Descent Grade Limit (between 0-10%), Road Grade Change Factor (between 0-100%) and manual Up and Down control. Notice that the Companion App has a slightly different functionality depending of what brand of trainer (TACX, Wahoo or FTMS enabled) is connected, due to specific connectivity differences. <br clear="left">

# FiTness Machine Service a Bluetooth Service Specification
From 2015 to 2017 the Sports and Fitness Working Group (SIG) designed a Bluetooth Service specification. This service exposes training-related data in the sports and fitness environment, which allows a Server (e.g., a fitness machine) to send training-related data to a Client. In Februari 2017 the service specification reached a stable version: [Fitness Machine Service 1.0](https://www.bluetooth.com/specifications/specs/fitness-machine-service-1-0/) when it was adopted by the Bluetooth SIG Board of Directors. Have a look at the document to appreciate the effort of all the contributors and the companies they represented!<br>
<b>FTMS</b> is an open (nonproprietary) protocol that is not owned by any particular company and not limited to a particular company's product. It can be compared in that respect with FE-C over ANT+, however <b>FTMS</b> is targeted to control fitness equipment over <b>Bluetooth</b>!<br>
According to the smart trainer recommendations guide winter 2020-2021 of [DCRainmaker](https://www.dcrainmaker.com/2020/11/smart-cycle-trainer-recommendations-guide-winter.html) the situation evolved:
>Meanwhile, for Bluetooth Smart, there’s FTMS, which is basically the same thing as FE-C when it comes to trainers. It’s not quite as widely adopted yet by trainer companies, but is by app companies. On the trainer company side only Elite, Saris, and Kinetic support it across the board. With Tacx having it on some but not all units, and Wahoo having it on no units (but all Wahoo and Tacx trainers support private Bluetooth Smart with all major apps anyway). Each year Wahoo and Tacx say they’ll get around to adding it to their higher-end units, and each year they don’t (practically speaking though, it won’t impact your app usage, since all major apps support Tacx/Wahoo variants anyway).<br>

|Trainer  |Supported protocols|
|---|---|
|Elite |ANT+ FE-C and Bluetooth Smart FTMS on all 2020 smart trainers.|
|Gravat |ANT+ FE-C and Bluetooth Smart FTMS on all 2020 smart trainers|
|JetBlack |ANT+ FE-C and Bluetooth Smart FTMS on all 2020 smart trainers.|
|Kinetic |ANT+ FE-C and Bluetooth Smart FTMS on all 2020 smart trainers.|
|Minoura |ANT+ FE-C and Bluetooth Smart FTMS on all 2020 smart trainers.|
|Saris |ANT+ FE-C and Bluetooth Smart FTMS on all 2020 smart trainers.|
|STAC |ANT+ FE-C and Bluetooth Smart FTMS on all 2020 smart trainers.|
|Tacx |ANT+ FE-C on all ‘Smart’ branded trainers (except Satori). FTMS on all non-NEO models.|
|Wahoo |ANT+ FE-C on all smart trainers, proprietary Wahoo Bluetooth Smart Control and all post-2020 models have Bluetooth Smart FTMS.|
|Zwift|ANT+ FE-C and Bluetooth Smart FTMS on Zwift Hub smart trainer.|
| | cf: [DCRainmaker](https://www.dcrainmaker.com/2020/11/smart-cycle-trainer-recommendations-guide-winter.html)|

# Sofar the good news!<br>
+ When a training app (like Zwift) has connected to your trainer using the FTMS protocol: is it possible to connect multiple devices via FTMS? As FTMS enables control of a physical device there can only be one <b>“controller”</b> to avoid safety issues. This means that you will not be able to connect multiple devices directly to the indoor bike trainer or treadmill using FTMS. If the trainer does not appear in an app’s (e.g. Zwift's) device list (on the Zwift pairing screen) it generally means the trainer is (still) connected to another controlling app or device. It is virtually impossible to connect the trainer to Zwift using FTMS, have a nice indoor ride and at the same time to connect for example the Simcline to the trainer or Zwift for simulating road incline..... A working solution is a Man-In-The-Middle (MITM)!
+ Notice that a fully working Simcline (acting as a MITM), supporting FTMS enabled Trainers, is up for grabs. Several trainers of very different brands have been tested successfuly by now, and you are invited to test the available code with your FTMS enabled Trainer.
# What about ANT+ (FE-C) and FTMS at the same time<br>
+ When a training app (like Zwift) has connected to your trainer using the ANT+ protocol: is it possible to connect other devices via FTMS?<br>
Since this ANT+ connection enables control of the physical device (trainer) there can NOT be connected another <b>“controller”</b> at the same time over FTMS to avoid safety issues. Only one (1) controlling app is allowed to connect and drive the Trainer at any time. You know, 2 captains on one ship is a recipe for disaster!
If this case, unfortunately and undesirebly, happens with your equipment setup the controlling Client-side code will not connect or disconnect with an error message! So keep these worlds separated! If you intend to use devices with BLE and FTMS: mechanically disconnect the ANT+ dongle to avoid your controller App (like Zwift) to (auto)connect over ANT+.
# Man-In-The-Middle (MITM) software pattern<br>
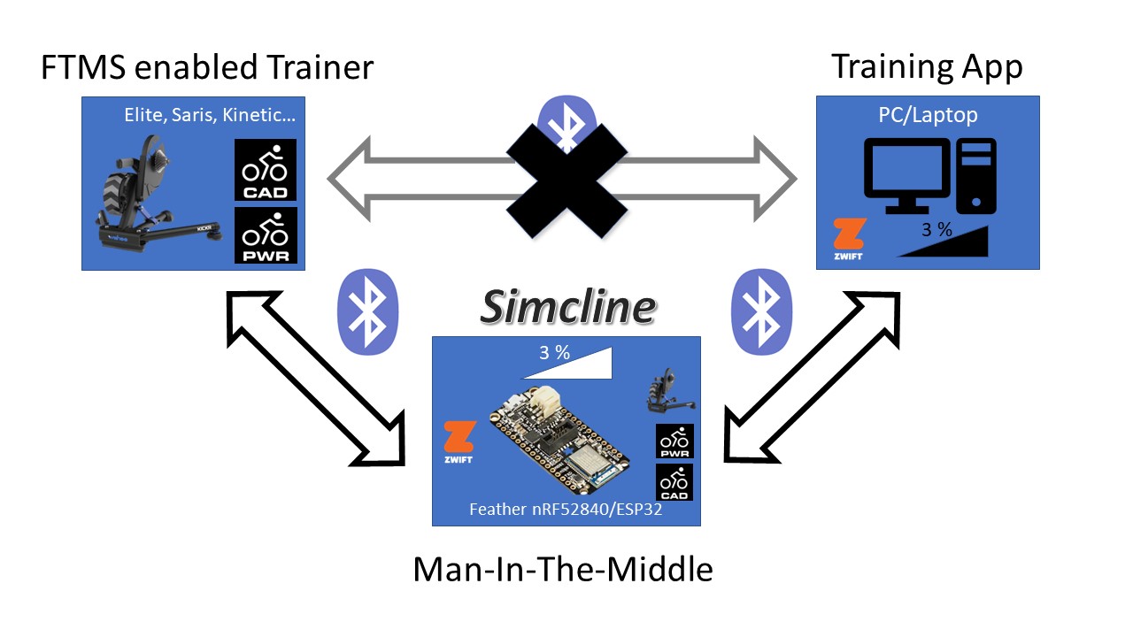
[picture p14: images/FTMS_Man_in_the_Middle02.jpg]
Man in the Middle
<br>
<b>Man-In-The-Middle</b> is a powerful software engineering pattern that is applied in many software designs. Unfortunately it is also known for a negative application in communication traffic: MITM is a common type of cybersecurity attack that allows attackers to eavesdrop on the communication between two targets.
We have applied the very principle: the Simcline is strategicly positioned in between the BLE communication of the FTMS enabled Trainer and the training App (like Zwift) running on the PC/Laptop, all communication traffic can be inspected in that MITM position, when it is passed on from one to the other, in both directions. When Zwift sends resistance information (like the road inclination) to the FTMS enabled trainer, this information can be intercepted and applied to determine the up/down positioning of the Simcline. <br>

# Choose a Development board: nRF52840 or ESP32?<br>
Until early 2023 the Simcline project (a.o.) solely worked with the <b>Feather nRF52840 Express</b> development board and the Bluefruit/Adafruit libraries. This is a very stable platform and gave reliable results during development and what's more during many indoor seasons of 5 hours per week operation! However, the MITM application and actuator control (a.k.a. Simcline) is at the capacity limits of the nRF52840 processor. 
See for a reliable and <b>proven</b> solution: [Adafruit Feather nRF52840 Express](https://learn.adafruit.com/introducing-the-adafruit-nrf52840-feather) <br>

So the question was raised why not use the <b>ESP32</b>, a series of low-cost and low-power System on a Chip (SoC) microcontrollers developed by Espressif that include Wi-Fi and Bluetooth wireless capabilities and dual-core processor? See for an introduction: [Random Nerds Tutorials](https://randomnerdtutorials.com/getting-started-with-esp32/). Particularly the multiprocessing capabilities of the dual-core processor make the ESP32 a very tempting option in this project!
To benefit of the same formfactor (fit with the Simcline 2.0 component box!), I decided to (re)produce the Simcline code with the [Adafruit Feather ESP32 V2](https://learn.adafruit.com/adafruit-esp32-feather-v2) for the <b>ESP32</b> platform. Just comparing the overal specs (on paper) of both processor platforms is not sufficient... one needs to take into account the (quality of the) available libraries as well to reach success. The 'standard' ESP32 Arduino <b>Bluedroid</b> library (for BLE support) turned out to be buggy! Fortunately [H2Zero](https://github.com/h2zero/NimBLE-Arduino) has created a more or less compatible replacement for Bluedroid, called <b>NimBLE-Arduino</b>! The application of <b>NimBLE</b> saved the porting of the software to the ESP32 platform! 
In week 7 of 2023 the ESP32 code reached a stable level and became publicly available for testing with FTMS-enabled trainer brands.

# How to start?<br>
+ Install the [Arduino IDE](https://www.arduino.cc/en/Main/Software) and all the libraries on a PC/Mac.
+ If you are using an ESP32 board then also download the ESP32 NimBLE library (<b>Version 1.4.3</b>), see [Arduino Installation NimBLE](https://github.com/h2zero/NimBLE-Arduino#arduino-installation)
+ Download all the code from [Github](https://github.com/Berg0162/simcline/tree/master/FTMS%20Enabled) and install. <br>

# How to make it work?<br>
The requirements in this phase are simple: 
+ running Zwift, Rouvy or myWhoosh app or alike, 
+ working Feather nRF52840/ESP32-V2 development board and 
+ a FTMS enabled Trainer.<br>

# Testing is Knowing!<br>
I can understand and respect that you have some reserve: Is this really working in my situation? Better test if it is working, before buying all components and start building.
In the Github repository (see above) you will find the appropriate files with code: <b>FTMS_Client</b> and <b>FTMS_Server</b>. It is coded with the only intention to check if the MITM solution is delivering in your specific situation.<br>

<b>What it does in short:</b><br>
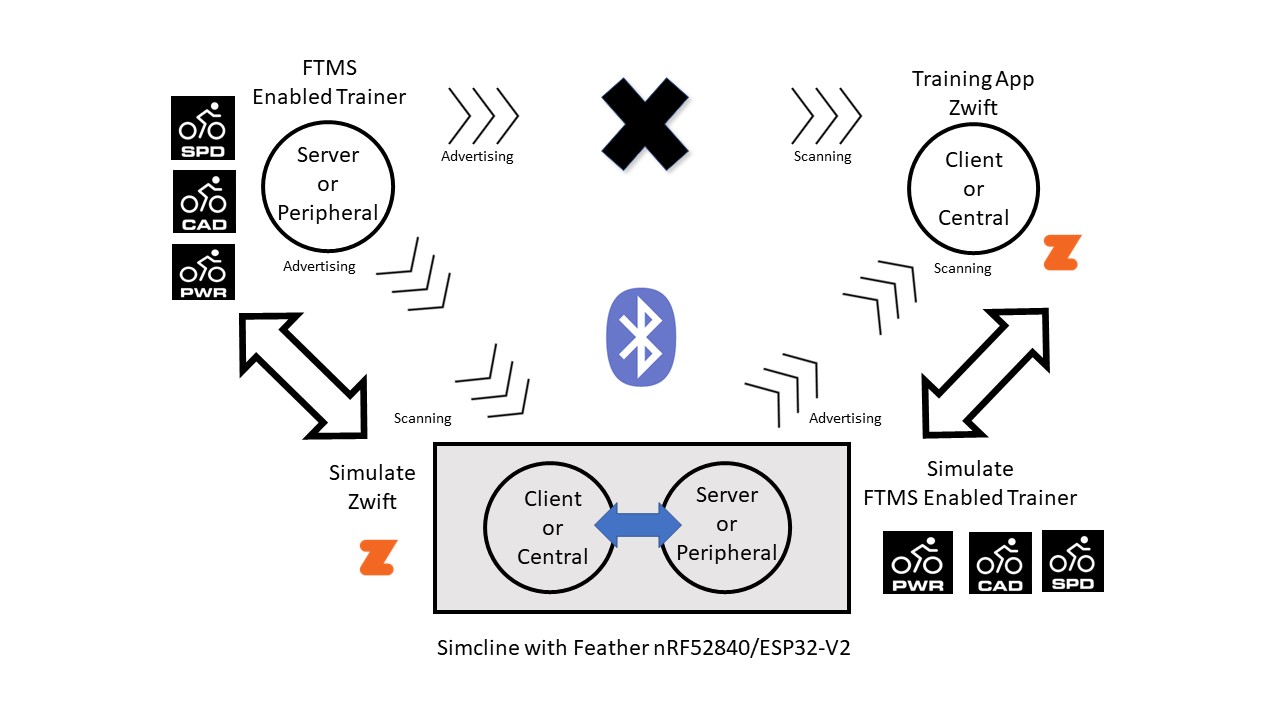
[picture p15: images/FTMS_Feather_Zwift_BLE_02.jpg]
Simcline in the Middle
<br>
A working <b>MITM</b> implementation links a bike trainer (BLE Server FTMS) and a PC/Laptop (BLE Client running Zwift) with the Feather nRF52/ESP32, like a <b>bridge</b> in between. The MITM bridge can pass on, control, filter and alter the interchanged trafic data! The <b>MITM</b> code is fully ignorant of mechanical or electronic components that drive the Simcline construction.<br>
```
It simply estabishes a virtual BLE bridge and allows you to ride the bike on the FTMS enabled Trainer and 
feel the resistance that comes with the route you have choosen, thanks to Zwift.
The experience should not differ from a normal direct one-to-one connection, Zwift - FTMS enabled Trainer!
```
All FTMS enabled indoor trainers expose your efforts on the bike in 2 additional BLE services: Cyling Power (CPS) and Speed & Cadence (CSC). These services are detected and applied by many training app's and are therefore an integral part of the present design of the MITM bridge. Training app's simply expect, when they connect to the FTMS enabled trainer, that the CPS and CSC services are available in one go! The Zwift pairing screen is a good example: it expects Power (CPS), Cadence (CSC) and a "Controllable" (with FTMS) to be connected...
+ The client-side (Feather nRF52/ESP32) scans for (a trainer) and connects with <b>FTMS, CPS and CSC</b> and collects cyling power, speed and cadence data like Zwift would do! The code with the name: <b>FTMS_Client</b> is doing just that at the left side of the "bridge"!
+ The Server-side (Feather nRF52/ESP32) advertises and enables connection with training/cycling/game apps like Zwift and collects relevant resistance data, it simulates as if an active <b>FTMS</b> enabled trainer is connected to Zwift or alike! Notice that the Server-side also exposes active <b>CPS</b> and <b>CSC</b> services. The code with the name: <b>FTMS_Server</b> is doing just at the right side of the "bridge"!
+ The <b>MITM</b> code is connecting both sides at the same time: a full-blown working bridge, <b>FTMS_Bridge</b><br clear="left">

<i>The test programs (FTMS Client, FTMS Server and FTMS-Zwift-Bridge) are only using Serial Monitor (screen output) to show what is happening!</i><br>
```
Please write down the MAC/Device Addresses of a) your FTMS enabled trainer and b) your Desktop/Laptop with Zwift. 
These are presented in the Serial Monitor log file when running the Client and Server test code.
```
<b>Use the code for reconnaissance and testing!</b><br>
Please follow <b>ALWAYS</b> the different usage instructions at the first part of the respective program codes!
+ Start your reconnaissance with running <b>FTMS_Client</b> and experience how your development board is controlling the resistance of your FTMS enabled trainer. Notice that this piece of code is highly dependent on the type and brand of FTMS enabled Trainer and therefore most critical!
+ Be aware of undesirebly <b>autoconnect</b> with your standard equipment setup using ANT+ or FTMS. The FTMS Client (or FTMS-Zwift-Bridge) will reach an error state that does not help you getting representative results during the reconnaisance! Once again: 2 captains on one ship is a recipe for disaster!
```
/* 
 *  This Feather nRF52840/ESP32 tested code scans for the CPS, CSC and FTMS
 *  that the trainer is advertising, it tries to connect and then 
 *  enables .....
 *  
 *  Requirements: FTMS trainer and Feather nRF52/ESP32 board
 *  1) Upload and Run this code on the Feather nRF5/ESP322
 *  2) Start the Serial Monitor to catch verbose debugging and data info
 *  3) Power ON and Wake UP trainer -> do NOT connect with other devices
 *  4) Trainer and Feather should successfully pair or disconnect...
 *  5) Keep the Serial Monitor visible on top of all windows 
 *  6) Move the trainer pedals and notice/feel changes in resistance...
 *     The Client sends Resistance Parameters to the Trainer that mimic 
 *     the riding of a road on rolling hills (max 6% grade)!
 *  7) Inspect the info presented by Serial Monitor.....
 *  
 */
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

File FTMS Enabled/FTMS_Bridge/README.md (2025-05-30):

# Changelog nRF52 FTMS_Bridge --> ESP-code is deprecated!

## v0.3.1
### Added or Changed
- Corrected unsecure use of sizeof() with string arrays! Feature: FTM, CP and CSC !!!

## v0.3.2
### Added or Changed
- Trainer.IsConnected = true only at the end of client_connect_callback to avoid cluttering of messages
- Inserted more selective setting of Connection Parameters at start of scanning and at start of advertising
- Inserted requestConnectionParameter after client connection and synch with poll_delay
- Inserted #define REQUEST_NEW_CONNECTION_PARAMETERS and allows for selective setting of ConnectionInterval

# Changelog ESP32 FTMS_Bridge

## v0.1.1
### Added or Changed
Changed Stack Depth values from 2048 to 4096 for Server Control Point Indicate (modified) and Write w Response

## v0.1.2
### Added or Changed
Inserted check (boolean) on Control Point Write-Response out of synch...

## v0.1.3
### Added or Changed
Cycling Speed Cadence Service changed to NOT Mandatory

## v0.1.4
### Added or Changed
Inserted checks on the input values of sensor location and location description array sizes (CP, CSC and HBM)

## v0.1.5
### Added or Changed
Corrected invalid (enable/disable) setting of HR measurement Characteristic in client_Set_All_NotificationIndication()<br>
Changed device identification naming to a simpler scheme: SIM32 or SIM52 instead of "Sim DevName"<br>
Server Characteristic values (read only) are now updated when a new client connection is established<br>
NimBLE registerForNotify() has been deprecated and is replaced with subscribe() / unsubscribe()<br>

### Removed
- Some older versions

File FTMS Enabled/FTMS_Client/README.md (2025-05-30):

# Changelog nRF52 FTMS_Client

## v0.3.6

### Added or Changed

- Inserted bool clientIsReadyToOperate instead of wait loop interval in setup()
- Inserted more selective setting of Connection Parameters at start of scanning
- Inserted requestConnectionParameter after client connection and synch with poll_delay
- Inserted #define REQUEST_NEW_CONNECTION_PARAMETERS and allows for selective setting of ConnectionInterval

### Removed
- Some older versions

# Changelog ESP32 FTMS_Client --> --> ESP-code is deprecated!

## v0.1.0
### Added or Changed
- Added first version

## v0.1.1
### Added or Changed
- Cycling Speed Cadence Service changed to NOT Mandatory

## v0.1.2
### Added or Changed
- Inserted checks on the input value of sensor location and location description array sizes (CPS, CSC and HBM)

## v0.1.3
### Added or Changed
- NimBLE registerForNotify() has been deprecated and is replaced with subscribe() / unsubscribe()
- Replaced Control point test data (Volcano Circuit) for steeper rolling hills to improve experience of pedalling resistance
- Added more DEBUG on/off selections to minimize serial output information overload
- Changed device identification naming to a simpler scheme: SIM32
  
### Removed
- Some older versions

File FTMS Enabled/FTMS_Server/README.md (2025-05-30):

# Changelog nRF52 FTMS_Server

## v0.3.1

### Added or Changed
- inserted missing (!) FTM ControlPoint set cccd callback
### Removed
- Deleted Wait timing in setup() after scanning!

## v0.3.2

### Added or Changed
- Added selective setting of preferred connection parameters before start of advertising
- Added in DEBUG mode printout of connection parametes
- Inserted selective use of requestConnectionParameter

# Changelog ESP32 FTMS_Server --> ESP-code is deprecated!

## v0.1.0
### Added or Changed
- Added first version

## v0.1.2
### Added or Changed
- Changed device identification naming to a simpler scheme: SIM32

### Removed
- Some older versions

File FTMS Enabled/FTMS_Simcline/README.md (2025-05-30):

# Changelog nRF52 FTMS Simcline

## v0.2.0

### Added or Changed
- Extra waiting directly after client connection, delay(poll_delay) moved after debug prints....
- Inserted full HBM support
- Corrected versions of client_enable and client_connect
- Corrected version of Indoor Bike Data
- updated with code of Client version 3.0
- Inserted setTxPower(4) after Bluefruit.begin() for scanning that was missing....
- Inserted Bluefruit.configCentralConn for central and peripheral
- Inserted Bluefruit.getName for determining the board name!
- changed filterRSSI to -80
- After Client or Server disconnect: scanning and advertising again!!
- Machine Status and Trainingstatus added missing if(...Chr.notifyEnabled)
- Inserted wait for connection in client_connect_callback 

## v0.2.1

### Added or Changed
- Corrected unsecure use of sizeof() with string arrays! Feature: FTM, CP and CSC !!!

## v0.2.2
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

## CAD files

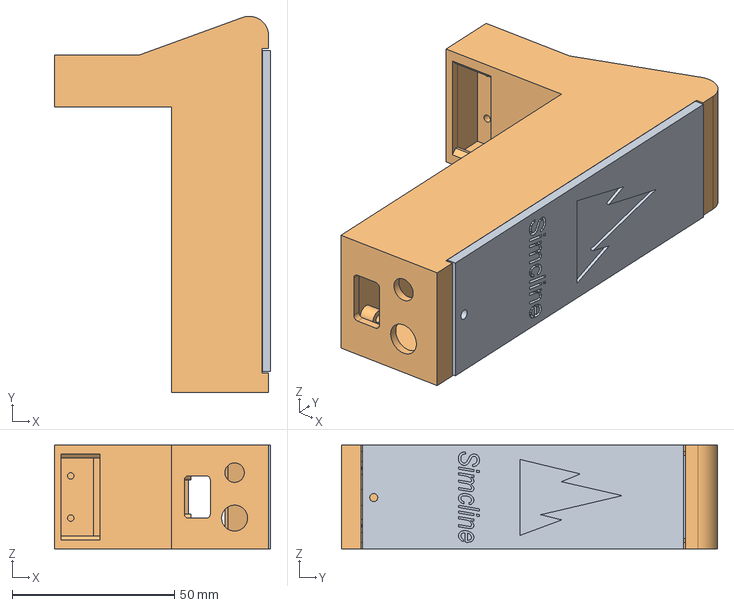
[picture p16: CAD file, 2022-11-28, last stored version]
docs/Components_Box_Complete_02.FCStd
66.6 x 116.0 x 32.0 mm
Closing Lid with screw hole

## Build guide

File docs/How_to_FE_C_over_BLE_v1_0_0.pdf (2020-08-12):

# FE-C over BLE

# Simple how-to for engineers

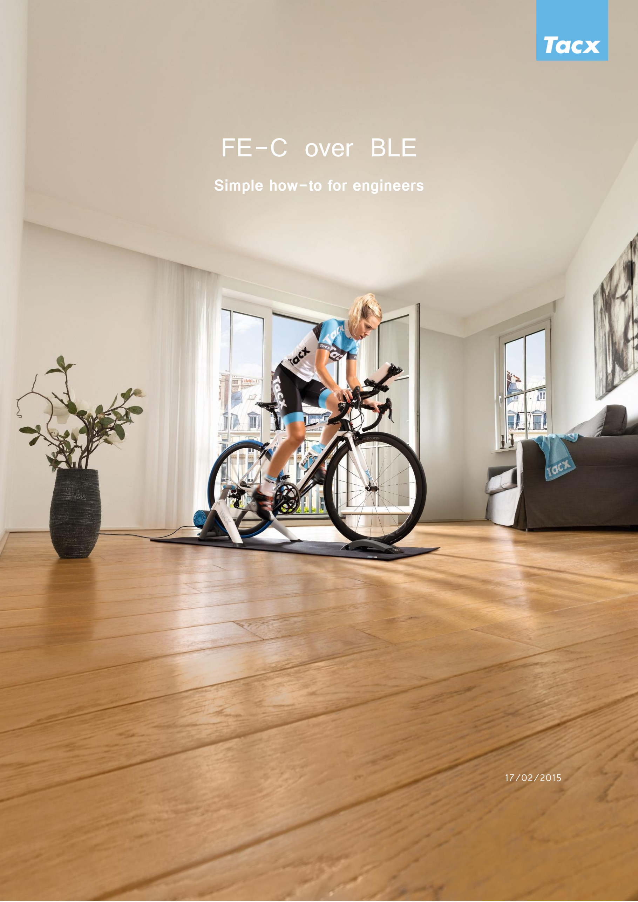
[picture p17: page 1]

1 | 17/02/2015 | FE-C over BLE

17/02/2015

# Introduction

This document will explain how to use the FE-C over BLE feature in Tacx Smart Trainers. Tacx designed this feature because Bluetooth is lacking open standard for trainers on Bluetooth.

It uses the ANT+ FE-C definition for the data content, but transports this data thru a BLE serial port service. Therefore a prerequisite for this technic is knowledge of the ANT+ FE-C protocol. A complete description of FE-C can be found at: http://www.thisisant.com/resources/fitness-equipment-device/

Revision | Effective Date | Author | Description
1.0.0 | 20-8-2015 | D. de Nijs | Initial release.

# Nordic Serialport Service

The transport method that is used is derived from the NordicUartService. This serial port service can basically send and receive arrays of data ranging from 1..20 bytes.

The only thing that is different is the service UUID and the two characteristics UUID’s these are renamed to the Tacx standard UUID with the specific part for the FEC service starting 0xFEC…

In the figure below the UUID’s are shown in there hierarchy order.

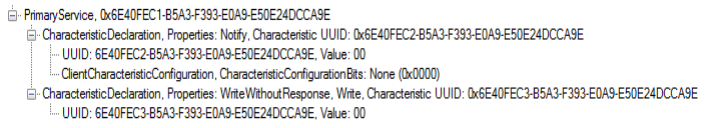
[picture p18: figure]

The 6E40-FEC2-B5A3-F393-E0A9-E50E24DCCA9E is the RX part of the service this characteristic will notify is the trainer sends out an packet(Notification must be turned on in the CharacteristicConfigurationBits).

Characteristic 6E40-FEC2-B5A3-F393-E0A9-E50E24DCCA9E is the TX part of the service, message that need to be send to the trainer can be written to this characteristic. The Ant+ FE-C wound exceed the 20 byte maximum , so there is no need to split message up in multiple sections.

The recommended rate of transmitting messages to the trainer is 4Hz since this is also the native rate over ANT. The trainer will also transmit messages with this rate.

# Datacontent FE-C

The data that is generated by the trainer, and the data that is send to the trainer consists of a complete ANT message.

An example of a message from the trainer can look like this:

A4094E05101904000000FF30

When the data broken up into hex values and interpreted as an ANT message it looks like this:

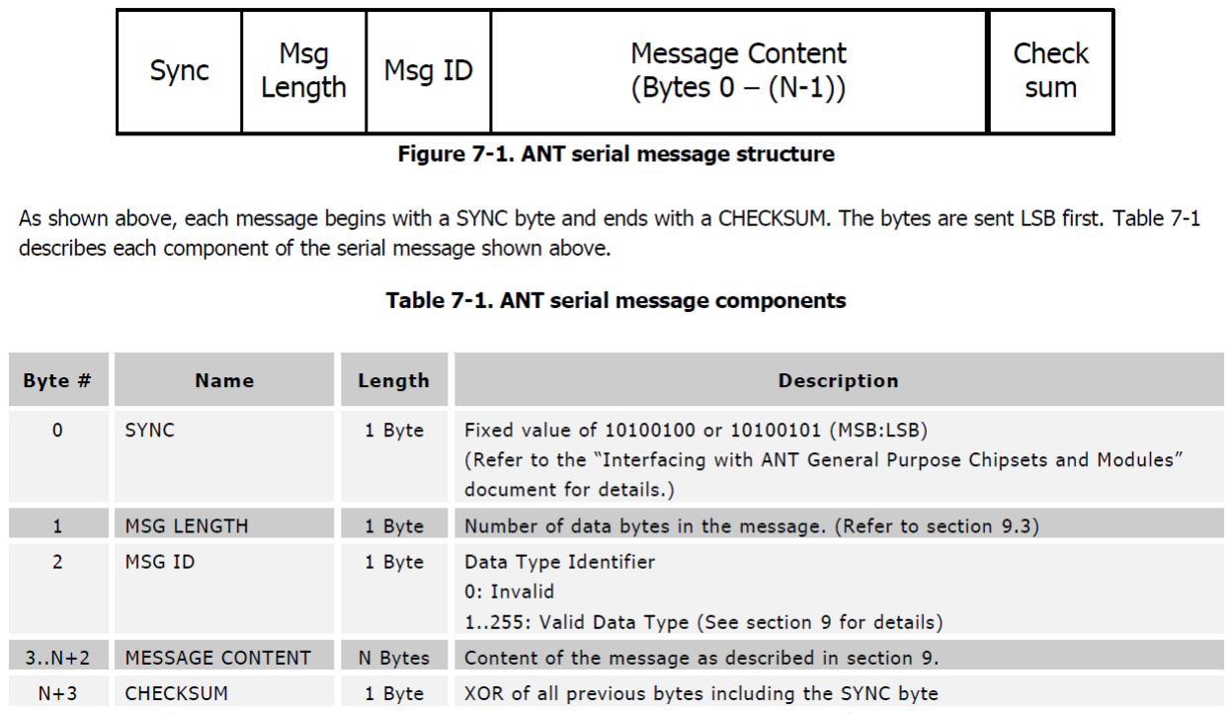
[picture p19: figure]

Section from document: ANT_Message_Protocol_and_Usage_Rev5.0.pdf

Example:

0xA4 | 0x09 | 0x4E | 0x05 | 0x10 0x19 0x04 0x00 0x00 0x00 0xFF 0x24 | 0x30
Sync | Length | Type | Channel | Data | Checksum
This message is a General FE Data page

The message will always start with 0xA4 this is the ANT sync character, followed by the length of the data + 1. The type can vary i.e acknowledged, broadcast.

The channel number is our case channel 5 but the channel number is ignored when a message is send to the trainer.

The channel number is followed by (length-1) data bytes, the message end with a checksum which is the sum of all bytes excluding the 0xA4 sync byte.

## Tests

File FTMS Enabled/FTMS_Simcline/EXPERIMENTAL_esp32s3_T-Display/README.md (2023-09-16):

# SIMCLINE Icon &nbsp; SIMCLINE for FTMS enabled Trainers <br> based on the LILYGO ESP32S3 T-Display board <br>(experiment in progress!)

## Description
T-Display-S3 is a ESP32-S3 development board. It is equipped with a color 1.9" LCD screen and two programmable buttons. Communication using I8080 interface. Retains the same layout design as T-Display. You can directly use ESP32S3 for USB communication or programming.

## LilyGo ESP32S3 T-display
This board and ESP32S3 processor was selected for its excellent specifications crisp and colorful display. Aside of gaining experience with the [TFT_eSPI](https://github.com/Bodmer/TFT_eSPI) library, creating a much richer visual user interface (than a SSD1306 0,96 Inch) was the dominant incentive. A lot of inspiration and practical knowledge was obtained by studying on Youtube: [the Volos Projects](https://www.youtube.com/c/VolosProjects). This ended up sofar in a good working and visually attractive Simcline 2.0 interface! What's more, in the experiments the processor was behaving like to be expected (despite the high display interface load) and I did not experience (during operation) any response difference with other ESP32 boards (with minimal display interface load) and that have been tested thoroughly...<br>
Unfortunately the LilyGo board does <b>NOT fit the original components box</b>, so that needs extra attention in the near future. Technically there is no reason sofar not to like this board!!!

## Arduino IDE 2.2
The present code is developed on Arduino IDE 2.2. Notice that you will need an Arduino IDE that is tailored for this specific <b>ESP32S3</b> processor!<br>

## Before you start
Please follow the installation instructions for the [ESP32S3 T-display](https://github.com/Xinyuan-LilyGO/T-Display-S3)<br>
If you select in the menu bar of Arduino IDE 2.2 <b>Tools</b>, the settings for the <b>ESP32S3</b> processor and the project are the following:
<p align=center>
S3-Switch
</p>
<br clear="left">

## T-Display-S3 Pinout
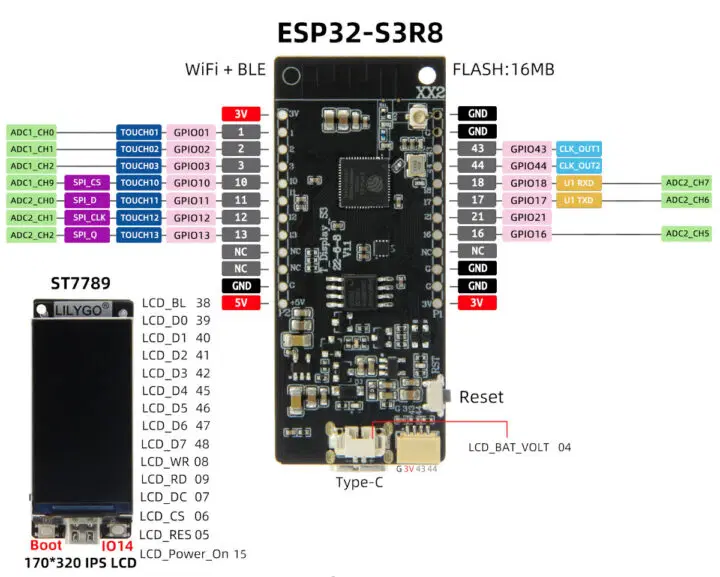
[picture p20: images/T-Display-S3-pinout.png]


## Quick Specs
- MCU: ESP32-S3R8 Dual-core LX7 microprocessor
- Wireless Connectivity: Wi-Fi 802.11, BLE 5 + BT mesh
- Programming Platform: Arduino-ide, Micropython
- Flash: 16MB
- PSRAM: 8MB
- Bat Voltage Detection: IO 04
- Onboard Functions: Boot + Reset + IO 14 Button
- LCD: 1.9" diagonal, Full-color TFT Display
- Drive Chip: ST7789V
- Resolution: 170(H)RGB x320(V) 8-Bit Parallel Interface
- Working Power Supply: 3.3V
- Supports: STEMMA QT / Qwiic
- Connector: JST-SH 1.0mm 4 PIN
- Dimensions: 62 x 26 x 10mm

# Electronic Components and Circuitry used in experimental version<br>
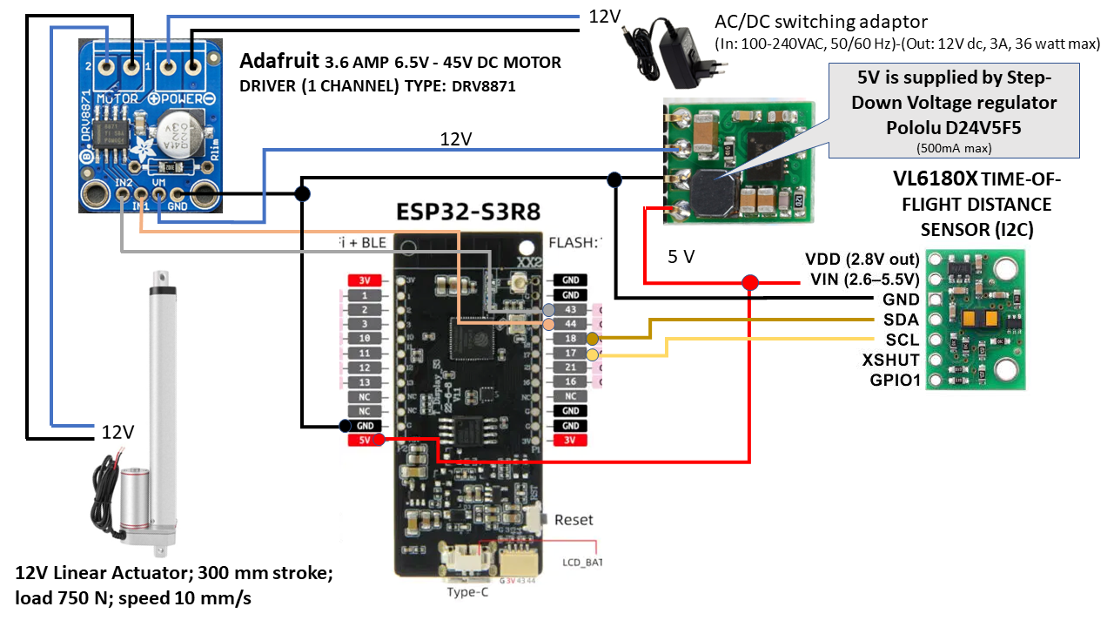
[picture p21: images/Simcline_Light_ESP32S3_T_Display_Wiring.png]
Circuitry version 2.0

I have chosen for the following 4 compact active components that are slightly different from the earlier SIMCLINE project:<br>
<b>Adafruit DRV8871 DC Motor Driver</b><br>
A small one channel motor driver for 12 V (6.5 - 48 V) and 3,6 Amperes max. This board enables the processor to set the Actuator motor in up or down movement. It transforms logical digital levels (Go Up, Go Down and Stop) from the Feather nRF52/ESP32 to switching of 12 Volt at 3,6 Amperes max., the levels at which the Actuator works. Notice that default the board comes limited to 2,6 Amperes and you need to add a resistor to set for max current level. Install Vertical Through Hole Male PCB Header Pins on the board; this will allow correct mounting of the board inside the components box!<br>
<b>LYLIGO ESP32S3 T-Display</b><br>
The programmed ESP32S3 is communicating with (a) the trainer to collect power output  information and (b) with the training App for resistance settings (like grade) or (c) with the Companion App on your mobile phone. The programmed ESP32S3 is in full control of the Simcline operation.<br>
<b>Pololu Time-of-Flight-Distance sensor VL6180X</b><br> The sensor board (12.7 * 17.8 mm) contains a very tiny laser source, and a matching sensor. The VL6180X can detect the "time of flight", or how long the laser light has taken to bounce back to the sensor. Since it uses a very narrow light source, it is perfect for determining distance of only the surface directly in front of it. The sensor registers quite accurately the (change in) position of the wheel axle during operation, by measuring the distance between the top of the inner frame and the reflection plate that is mounted on the carriage. The distance feedback of the sensor is crucial for determining how to set the position of the carriage and axle in accordance with the grade information that for example Zwift is using to set the resistance of the trainer. NOTICE: a) VL6180X boards are also offered by different suppliers and have different formfactors; b) Install Straight Angle Through Hole Male PCB Header Pins on the board; this will allow later flat mounting of the sensor board in the components box!<br>
<b>Pololu D24V5F5</b><br>
This is a small 5V, 500mA Step-Down Voltage Regulator that is responsible for voltage conversion from 12V to 5V, the power supply for all components boards. NOTICE: Install Straight Angle Through Hole Male PCB Header Pins on the board; this will allow later easy mounting of the sensor board in the components box!<br>

All components are documented very well and are low cost. There are lots of examples for use in an Arduino environment. They have turned out to be very reliable. The exact wiring of the components can be followed in the figure above.<br>

## Experimental Setup
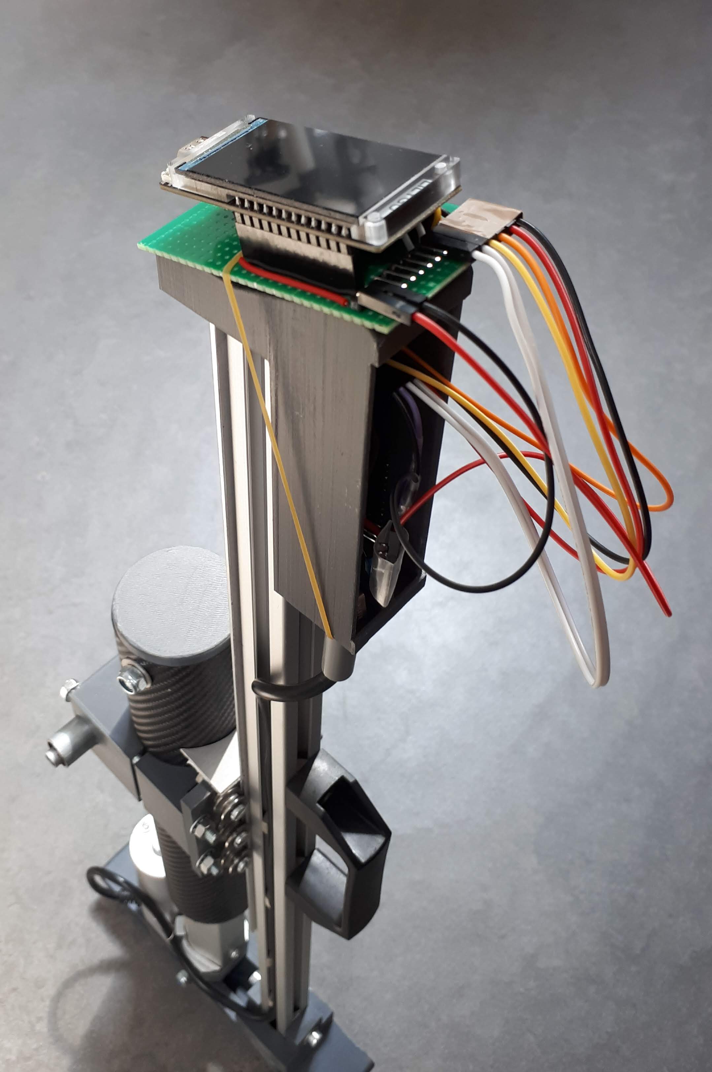
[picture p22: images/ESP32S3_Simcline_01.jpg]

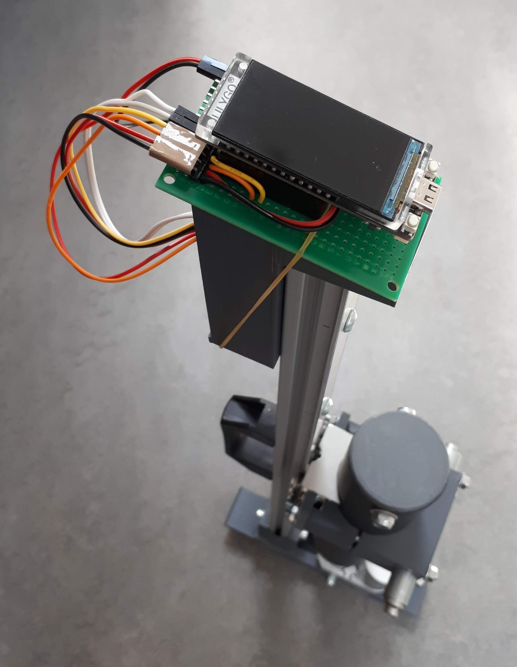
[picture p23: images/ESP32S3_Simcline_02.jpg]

<br clear="left">

## Display during a ride
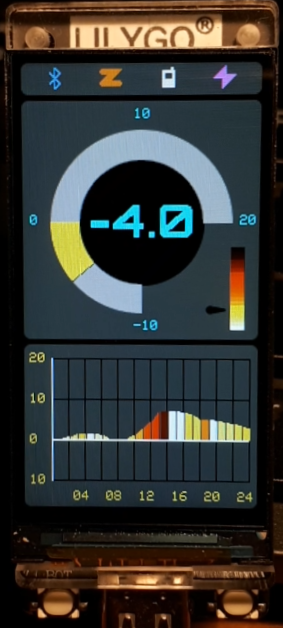
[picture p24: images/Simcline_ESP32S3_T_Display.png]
<br>
- Icons bar on the top shows active connections
- Actual road grade is shown in digits in the center of a gauge
- Gauge shows clockwise, positive up-hill-grades and counter clockwise, negative down-hill-grades
- Road profile is refreshed with every event (i.e. change of road grade) and shows the last 24 events
- Position in vertical color palette legend is dynamically shown
- Color palette for grade percentage is taken from [www.CylingCols.com](https://www.cyclingcols.com/col/Angliru).
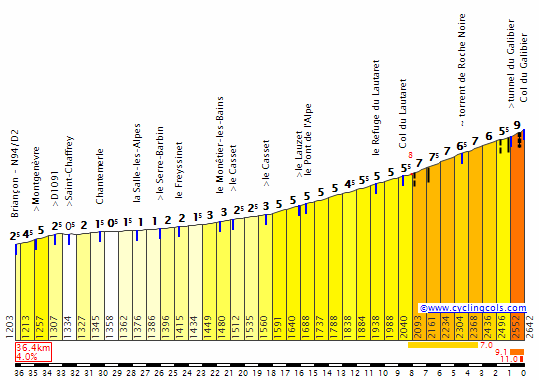
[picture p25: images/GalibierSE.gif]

<br clear="left">

## Video of display during fictional riding
Notice that the road inclination data were randomly generated (between -10 and +20) in a pace that one will never meet in the real world, just to show the interface during a long ride!
[See video on Youtube](https://www.youtube.com/watch?v=asnAkheFVb0&t=11s)

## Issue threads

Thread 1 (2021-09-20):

Fail message in Arduino IDE

Bigcogdog, 2021-09-20:
hi.
im very new at this and this project got me into arduino so here i am struggeling and im getting this messege when compilling the code:

Arduino: 1.8.16 (Windows 7), Board: "Adafruit Feather nRF52832, S132 6.1.1, Level 0 (Release)"

try_one:56:10: fatal error: Lifter.h: No such file or directory

   56 | #include <Lifter.h>

      |          ^~~~~~~~~~

compilation terminated.

exit status 1

Lifter.h: No such file or directory

This report would have more information with
"Show verbose output during compilation"
option enabled in File -> Preferences.

Berg0162, 2021-09-21:
Although verbose, the Arduino Error message is very clear: Your (Arduino IDE) Libraries directory is missing a critical file that references to the Lifter library. It fails to find the requested file: <Lifter.h> and probably (later in the compiling process) <Lifter.cpp>   ----> Solution: copy ALL the content of the code in the Github <libraries> directory (subdirectories AND their files) to the Arduino IDE <libraries> directory.

Bigcogdog, 2021-09-21:
Would it possible to contact you on mail? you can mail me at, mads-kudsk@hotmail.com to start a correspond

Berg0162, 2021-09-22:
For the time being, let's use this communication channel and see where it brings us!

Bigcogdog, 2021-09-22:
Okay, very well.. Let me be honest, I am a builder with my hands and not very firm with a computer and this project is my first and I know it might be a little ambitious but I would really like it to work, I have everything sorted, tacx hometrainer, the system wired up and the simcline build. The only thing missing is the system on the adafruit board.. Is there a way to get the adafruit with the codes on from you?
-Thanks Mads

Berg0162, 2021-09-22:
Ok Mads, that sounds like a worst case scenario! And we shouldn't start there! You are so close and I am convinced you can upload the Feather board with the code all by yourself! On your Windows PC find (with Explorer) the following path:  > This PC > Documents > Arduino
That Arduino directory is where the Windows Arduino IDE stores all the user generated program code. When you visually scan that Arduino subdirectory you will see the names of program code that you somehow created before, possibly there is also a subdirectory called **libraries**. The path looks like this:  > This PC > Documents > Arduino > libraries
In the error message from above that is exactly the place where the Arduino IDE was looking for a subdirectory called **Lifter**, containing a file called **Lifter.h**.
How to get things now up and running?
All you have to do is, copy **ALL** the contents of the **Github Arduino file directory** to the **Windows Arduino file directory** of your PC. Apparently you have succeeded in downloading some code from Github in that Windows Arduino directory, otherwise you would not have had that error message. So you are capable of downloading a file from Github to that Windows Arduino directory. In the end your Windows Arduino directory should be an exact copy (directory names and file content) of the Github Arduino directory.
In the Windows Arduino IDE select: File > Sketchbook and you will see not only the Simcline_v03 code but also the test programs that are helpful with testing your configuration.
Now start simple: try compiling and uploading to the Feather board for example the I2C_scanner and then the OLED_SSD1306 test programs....
Succes!

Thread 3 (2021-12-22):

correlation between actuator linear vs slope

cherryphilip74, 2021-12-22:
Dear Jörgen!

I'm back again with a couple questions. First I tried to study the simcline  flowchart just to adopt it on my chassis.
I understood the correlation between counts / slope % / VL6180 reads height to target /height of the fork wheel from gound.

I adopted these concepts also on my chassis (aluminum + 3d printed abs) just to create a simple solution without wood.
In general it works well, the flat position is correct but when slope value increases above 3.2% the equipment is not alligned with the software of the trainer.

Inside spreadsheet you can find all values related to VL6180 readings, slopes and wheel support to ground height.

Could you tell me what I'm doing wrong?

Thanks angan for your answers

Best Regards
Filippo

[SimCline.xlsx](https://github.com/Berg0162/simcline/files/7763674/SimCline.xlsx)

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

cherryphilip74, 2021-12-26:
Update
With TACX Trainer App it works fine between -5% and 16%, simcline monitor showing the same slope indicated on screen desktop, while with Rouvy App after 5% I observed a misalignment. I will try also Zwift app soon

Berg0162, 2021-12-27:
It is impossible for me to comment on these values since I have no inside knowledge of your construction and/or software... Which components have been applied? Is the Time-of-Flight sensor (short or long distance type?) carefully aligned? How is the code modified? What code settings are you applying? Etcetera.
I have a suggestion: please have a look at this: https://github.com/Berg0162/simcline/blob/master/README.md#simcline-in-tts4-controlled-operation
The training apps you have operational might very well be not WYSIWYG!

I compliment you with your mechanical design, it really looks robust. Have fun with it! Many nice indoor rides!

cherryphilip74, 2021-12-27:
Dear Jörgen!
Yes, i changed some values in according to my climb equipment.
I'm happy to share with all community my design (2 versions, the first with 250mm actuator linear and the other one of 300mm).
I used all components listed on your main page of simcline project, but i made also a specific pcb with leds and push button reset (i would like to make a complete board with motor driver included), see picture below.
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

Here some details:

RGVMAX, RGVMIN, aRGVmax e aRGVmin values parameters:
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

Maximun extension with hardware stopping:
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

iMax & iMin map:
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

aRGVmax & aRGVmin map:
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

Excel table based on the parameters set above:
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

Heights fork wheel to ground (max, flat and min height):
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

details about board and VL6180X sensor
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

Hardware tested with:
BKOOL --> Its ok
TACX --> its ok
ROUVY --> Not ok, disalligment
here some pictures:

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

Let me know if I have done something wrong and if so what to correct.

Best Regards
Filippo

GrepNatural, 2021-12-27:
Dear Filippo

in short, the ROUVY does not send the same values from the application about the gradient into the trainer. I have asked them and they do not say if is truth or not, becuase of company policy.

 there is my summary of the findings:

- TACX application very preciselly sets  incline/decline values on the SimCline and the values set in the application are set immediatelly also on the SimCline.

- Zwift has the incline/decline value shown in integer, so we cannot speak about precize setting of the incline/decline value from rider point of view, but the incline value approximattely corresponds what is set/shown on the SimCline.
But! the Zwift decline value is unexpetidly devided by 2! Thi is confirmed also by my colleague with Wahoo Climb device.
What I also noticed in the Zwift, that the SimCline response on change of the gradient in the application is very slow. I would guess that Zwift is sending the value delayed.
I did all the test on 'Alpe du Zwift' ride.

- ROUVY sets the values up to +/- 4% the same also on SimCline but then the values do not significantly corresponds. Eg. with 10% shown in the ROUVY application, the SimCline is set only to 8% and for 13% is there only aprox 10% set.
The advantage of Rouvy is that the values are changed fluently and quickly and the values are shown in 1/10 of %

I am very surprise that both the applications do not set the gradient to the trainer equally with what is shown to the rider.
I have asked my colleague to check my findings with Wahoo Climb on the ROUVY as well.

Thanks Martin

cherryphilip74, 2021-12-27:
Hi Martin,
your feedback is reassuring to me. I too find the same values with Rouvy, 10% set in the ROUVY application, the SimCline shows only 8% and for 11% it is only show to about 8.5%. This is valid only incline positive, in decline it seems aligned (tested up to -3.5%).
Yesterday and today, I've tested:

•	TACX application, I confirm that it's very precisely sets incline/decline values on the SimCline and the values set in the application are set immediately also on the SimCline

•	BKOOL application, also this application seems very precisely and having same TACX app characterizes.

It took me a long time just to find the correct setting and I understood later that a possible issue could be associated with the Rouvy app.
I think that i find the right setup for my hardware, I will do other tests with BKOOL and TACX only and then will be release the project on my github/cherryphilip74 for the community.
I big thanks to Jörgen for this opportunity and for the patience for the countless messages.

Best Regards
Filippo

wells240, 2021-12-28:
Nice work Filippo
I'm also working on Simclin project.
I keep Jörgen very busy :) He is a great help and I appreciate it very much.

Berg0162, 2021-12-28:
Dear Filippo,
I have carefully looked at how you have modified some of the critical settings in the Simcline code to suit your setup. I do not see any irregularities or inconsistencies that should bother you or disturb a smooth working of the code. None of these settings can be responsible for the discrepancies that you (and many others) came across with respect to WYSIWYG for road inclination!
By the way nice clean solution with that PCB, compliments! What software have you used for the PCB design and where did you have it produced?
Best wishes,
Jörgen.

wells240, 2021-12-28:
Jörgen,
This mail was not for me

Le mar. 28 déc. 2021 03 h 09, Jörgen van den Berg ***@***.***>
a écrit :

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

Berg0162, 2021-12-28:
You are right but you are a member now of this thread and you will see all comments..... that is a feature not a bug!

cherryphilip74, 2021-12-28:
> Dear Filippo, I have carefully looked at how you have modified some of the critical settings in the Simcline code to suit your setup. I do not see any irregularities or inconsistencies that should bother you or disturb a smooth working of the code. None of these settings can be responsible for the discrepancies that you (and many others) came across with respect to WYSIWYG for road inclination! By the way nice clean solution with that PCB, compliments! What software have you used for the PCB design and where did you have it produced? Best wishes, Jörgen.

Dear Jörgen!

thanks for your feedback.
I confirm that my hardware with TACX and BKOOL respects the WYSIWYG  rule (error within +/- 2-3mm sometimes also no error).

Regarding to PCB design, i use [easyeda](https://easyeda.com/editor) the suite complete for design (easyeda)/manufactuing (JLPCB) and components (LCSC). It's possible to produce assembled or pre-assembled PCBs.

If you want I can be happy to help you with the design (this is my job) or to take the first steps (here my email cherryphilip@email.com)

For me this trend may be closed

Best wishes,
Filippo

Closed 2021-12-29.

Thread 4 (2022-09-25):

Elite Trainer code

cherryphilip74, 2022-09-25:
Dear Jörgen!
I came back here, but today not for an issue regarding the my SimCline simulator (it works fine!).
Recentelly I bought a new Elite Direto XR-T trainer for my new SCOTT ADDICT RC bike and i saw that SimCline now is availble also Wahoo trainer and of couse TACX too.
So, I would like to contribute to the development of SimCline for ELITE if you plan to do it, so that SimCline can communicate with the best trainers on the market and to be a reference for us.

Let me know how I can be useful

Best Regards
Filippo (cherryphilip)

cherryphilip74, 2022-10-02:
Dear Jörgen!

of course I'm serious ;-)
Only today I was able to work. I received the trainer last thursday and up to yesterday I was busy with my family.
Before to all I did a compare with nRF App between TACX and ELITE code , and with suprise they are similar (same root).
After the nRF check, i modified the ino file  "Test_FE-C_over_BLE"
with correct UUID's and here the serial output and display output:

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

Next step to change the UUID on the main program and let's see how SimCline responds and also SimCline companion App

Regards
Filippo (cherryphilip)

cherryphilip74, 2022-10-08:
I tried to change Tacx's UUID with Elite in main program.. unfortunately it not works (not read page 51).
Any suggestions or can I close the issue?

Berg0162, 2022-10-08:
Dear Filippo,

I tried to change Tacx's UUID with Elite in main program..

Did you monitor the Serial Output of the Simcline code? Does it look like
the output of "Test_FE-C_over_BLE" ?

> unfortunately it not works (not read page 51).

Do you mean that you do not get a response (from Elite trainer) when the
code sends "request for data page 51". The previous sample output (test
program) did not  show a response on the page 51 request...

Any suggestions or can I close the issue?

If they do not have implemented the full FE-C protocol, what about other
(open source) protocols that Elite has implemented? How has Elite
implemented the communication with their Rizer product?

Best wishes,
Jörgen

Op za 8 okt. 2022 om 11:58 schreef cherryphilip ***@***.***>:

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

Berg0162, 2022-10-16:
I am curious about your answer and the present status!

Berg0162, 2022-10-16:
After some thought: I suggest that you try the following setup:
1) Connect the trainer exclusively over ANT+ with Zwift
2) Ride the Volcano route (number 1 in the list), road grade changes quite quickly after the start
3) Run the code "Test_FE-C_over_BLE" and
monitor the output for grade information after a request for Page 51

Possibly you tested previously only connecting the Direto over BLE with Zwift. Connecting over ANT+ with Zwift might change the way the Direto code handles and stores information... Testing is knowing!

cherryphilip74, 2022-10-16:
Hello Berg0162,

As I wrote in my first post, I ran the code "Test_FE-C_over_BLE" and then read the serial output (see photo), with no information from page 51.
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

Probably as you told me I only used the nREF card with the Elite trainer without ZWIFT connection.

Ok I can try as you suggested

BR
Filippo

stefaandesmet2003, 2022-10-16:
Hi,
I have a direto, not direto XR, and it doesn't support FEC over BLE. Page 51 request is typical ANT+ FEC.
Direto does have FTMS (0x1826), CPS (0x1818), CSCS (0x1816). And then DFU for firmware update, and an 'unknown' BLE service, for which I only discovered pedal stroke analysis data, no idea if this service offers anything else. I believe Direto XR will be identical, and may explain why you get no response for ANT+ style commands.
When connecting Zwift over ANT+, Zwift sends page 51 with a simulated slope (and not page 48 for example with the basic resistance level).
No idea what Zwift sends when connecting over BLE. There is a 'set target inclination' command within the BLE FTMS, but on direto it's not supported (read the fitness machine feature characteristic to check on direto XR). So probably Zwift sends a basic resistance command here.
@Berg0162 as I wrote to you separately, you may have to subscribe to the IBD notification on BLE, and pick up the target resistance level, and make a reverse calculation to translate to inclination on the simcline.
Possibly the 'set target inclination' command is implemented on the Elite Rizer.

Berg0162, 2022-10-18:
Thanks for the very helpful info!
Do not spend any time (anymore) on FE-C over BLE! All Elite trainers support FE-C over ANT+ only (!) and FE-C over BLE is definitely not supported by Elite on any of their trainer products. FE-C over BLE (conforming ANT+) is exclusively supported by TACX. See for a list of supported protocols: https://www.dcrainmaker.com/2020/11/smart-cycle-trainer-recommendations-guide-winter.html
My strategy now is to code a MITM for (open standard) FTMS and use the eavesdropped Grade info, that a trainer app (like Zwift) is sending, to drive the Simcline device up and down. That strategy worked well before with the Wahoo Kickr proprietary protocol.....
It will take an undetermined amount of time, patience and no garanties are given!
I will contact you when I need help and/or additional Elite Direto XR specific info!
Beste wishes,
Jörgen.

cherryphilip74, 2022-10-18:
 

Hi Jorgen! 
I understand and it's not easy to implement soon. I did see the DC RAINMAKER post you shared with me and also looked at this related trend on FE-C over ANT+.
https://github.com/laberning/openrowingmonitor/discussions/71

Thank you that you will keep me in case of help and / or further specific information on Elite Direto XR!

Best Regards

Filippo

Sent: Tuesday, October 18, 2022 at 11:34 AM
From: "Jörgen van den Berg" ***@***.***>
To: "Berg0162/simcline" ***@***.***>
Cc: "cherryphilip" ***@***.***>, "Author" ***@***.***>
Subject: Re: [Berg0162/simcline] Elite Trainer code (Issue #4)

Thanks for the very helpful info!
Do not spend any time (anymore) on FE-C over BLE! All Elite trainers support FE-C over ANT+ only (!) and FE-C over BLE is definitely not supported by Elite on any of their trainer products. FE-C over BLE (conforming ANT+) is exclusively supported by TACX. See for a list of supported protocols: https://www.dcrainmaker.com/2020/11/smart-cycle-trainer-recommendations-guide-winter.html
My strategy now is to code a MITM for (open standard) FTMS and use the eavesdropped Grade info, that a trainer app (like Zwift) is sending, to drive the Simcline device up and down. That strategy worked well before with the Wahoo Kickr proprietary protocol.....
It will take an undetermined amount of time, patience and no garanties are given!
I will contact you when I need help and/or additional Elite Direto XR specific info!
Beste wishes,
Jörgen.

—
Reply to this email directly, view it on GitHub, or unsubscribe.
You are receiving this because you authored the thread.Message ID: ***@***.***>

Berg0162, 2022-11-08:
Dear Filippo,
I have just posted a first Client-side FTMS version in: https://github.com/Berg0162/simcline/tree/master/FTMS%20Enabled
Follow the instructions at the start of the program and show me what is produced on the Serial Monitor output in the first pages. If all goes well the code should run for a longtime...... and only the start is critical!
Good luck!
Best wishes,
Jörgen.

Berg0162, 2022-11-14:
Dear Filippo,
Hopefully you received the previous post.....
I very much would appreciate that you test the FTMS_Client_v01 code with your Elite Direto trainer and supply me with the Serial Monitor output during the first minutes....
Beste wishes,
Jörgen.

cherryphilip74, 2022-11-17:
Hi Jörgen!

Here below the serial monitor output and a simple screenshot of the Zwift app during a workout. I used the Test_FTMS_Client_plus_CPS_CSC_v01.ino
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

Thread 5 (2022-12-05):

Testing Simcline with FTMS v01

cherryphilip74, 2022-12-05:
New section for Tread testing Simcline with FTMS v01
For a fast feedback (if you want) I created a private group in telegram (here link https://t.me/+FBKaD3Kue2Q5MzM0).
I will delete the link once time you joined it.

Can I close the previous Trainer Elite code section?

Berg0162, 2022-12-05:
Great! Sorry, I am not a Telegram user...
Yes, you can close the previous Issue!
You will be hearing from me!
Regards.

Op ma 5 dec. 2022 10:28 schreef cherryphilip ***@***.***>:

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

le-joebar, 2022-12-05:
Hello,

I have been busy reading you for several days.
I have a new Zwift Hub. I also do development with ESP32.
So I am familiar with this environment.
If I order a Bluefruit NRF52, would you be willing to try developing for this trainer?

Thank you very much for your answer.

Joel

le-joebar, 2022-12-05:
Thanks Jörghen,

I'm wait to see.

Best regard

Joel

Le lun. 5 déc. 2022, 16:15, Jörgen van den Berg ***@***.***>
a écrit :

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

Berg0162, 2022-12-05:
Dear Joel
If I order a Bluefruit NRF52, would you be willing to try developing for this trainer?

It is virtually impossible to develop specifically for all trainer brands. TACX and Wahoo are market leaders with a very large installed base and most of their smart trainers should work with the respective Simcline code versions! FTMS enabled Trainers is another large group of trainers that most likely will work (after this development) with the Simcline FTMS code version. No promises, No garanties!
According to DCRainmaker the Zwift Hub (see review on his site) has FTMS implemented. So in principle your Zwift Hub should work with the present FTMS code...after succesfull development!
There is only one way to be sure: testing is knowing! No promises, No garanties!

I don't have a BuethootBLE entry on my desktop.
Is it a problem?
Currently my config is a Desktop ANT+, Zwift companion.
So my setup is:
Pc connected to the Zwift Hub in Ant+ and bluetooth is free.

FTMS is only working over BLE (by design: bluetooth service) and with BLE enabled PC/Laptop/Tablet at one end and the FTMS enabled trainer at the other end. The Simcline with MITM code is in between. So if you do not have a BLE enabled device of the type PC/Laptop/Tablet (running the control software, Zwift/Rouvy/et cetera), it is never working with FTMS!

I have one more question!
Does the FTMS trainer work if I connect in BluethootBLe on the Zwift Companion or just connect the trainer by Ant+ to the PC and via the BluethootBLe on the Simclim via the client?

As far as I understand what you suggest, the answer is simple: no that will not end up in a working Simcline that catches Grade info from Zwift. The reason is that there can be only one controller (Training/Game app) that drives the trainer. That controller is working over ANT+ or (that is an XOR!) over BLE using FTMS.

Regards,
Jörgen.

cherryphilip74, 2022-12-06:
Have you considered using a D1 Mini NodeMCU ESP32 WiFi and Bluetooth BLE?
Link here: https://amzn.eu/d/2XgwXKY

ESP32 and nRF52 can do WiFi, Bluetooth Classic, and Bluetooth Low Energy (BLE), so seem are equivalent.
Are there technical limitation can't be applied to ESP32?
ESP32 is cheaper than nRF2 also low dimension

Best Regards
Filippo

le-joebar, 2022-12-06:
Dear Jörghen,

Ok I understand.
I will order a BluethootLE dongle for the PC.
I ordered the NRF I will do a series of tests as soon as I receive it.

Joel

Berg0162, 2022-12-06:
Dear Joel,
Let me hear what your experience is using the Client, Server and Bridge test codes with a Zwift hub at the other side!
Best wishes,
Jörgen.

cherryphilip74, 2022-12-07:
Dear Jörgen!
I tried today the first version of simcline with FTMS.
**Simply Wow**
Indoor apps support: Zwift, Rouvy

                               **Booting phase and pairing**

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

                               **Motor functionality error**

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

                               **No Rouvy app started**

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

                               **Paired with Direto Sim trainer**

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

                               **Rouvy app ready to ride**

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

                               **Rouvy app and Direto Sim trainer disconnected**

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

**Big varation of grade percentage between SimCline and Zwift, while those variation is low with SimCline and Rouvy.
Details reported on serial monitor see "new grade percentage section", grade value data from app reported inside  << grade>>**

                               **SERIAL MONITOR**
18:51:20.421 ->      <<--  SIMCLINE supporting: CPS, CSC and FTMS   -->>
18:51:20.421 -> ------------------------- Version 01.0 -------------------------
18:51:20.421 -> Simcline equiped with: Feather nRF52832
18:51:20.469 -> Feather internal Get & Set PRSdata to Max: 21600 Min: 19300 Perc.: 100 Displ.: 2
18:51:20.469 -> SSD1306 OLED display is running...

                               << Did you disable the basic motor functionality? >>

18:51:24.343 -> Simcline >> ERROR << Basic Motor Funtions are NOT working!!

                               << any moviment >>
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
cherryphilip74, 2022-12-09:
Dear Jörgen,

my comments in **bold**

> Dear Filippo, I am very happy with the results! It looks like the Simcline_FTMS is working very well with your Elite. A few minor points like not correct handling of long device names for the Oled display (only 10 char positions) was already corrected in the version 1.1 that I prepared the last days.
>
> **"18:51:24.343 -> Simcline >> ERROR << Basic Motor Funtions are NOT working!!"** Please do not blame the messenger! The code is testing the actuator + Time-of-Flight-sensor assembly for correct functioning by moving it up a determined distance and check exactly the end result. Then it sets a movement down and checks the end result! If this is not working 100%: you will get the error message and any further use of the actuator is blocked...(To avoid damaging the setup!) You know the drill from your Simcline usage (with TACX) in the past. If one gets this message you have to troubleshoot the involved components and check carefully their assembly in your setup! So please use the test-programs that can be accessed in the Simcline repository.... Let me guess: you have forgotten to plugin the 12V DC power for the actuator... Afterall the board (+Oled+ToF-Sensor) is powered (5V) over the USB connection (needed for the Serial Monitor) with your PC/Laptop, so that is working properly but the actuator is not moving (no power) when requested in the test code --> Error message!

**I'm forgot to change the highest and lowest value for microswitch activation, now motor works fine
#define MINPOSITION 18 // VL6180X highest value top microswitch activated to mechanically stop operation
#define MAXPOSITION 243 // VL6180X lowest value bottom microswitch activated to mechanically stop operation**

> I am puzzeled by your comment: **lost power & cadence signal** What was happening? How did you know? Please be more specific and detailed about what you observed!

**During the ride just to test simcline with ftms, the data field (Rouvy) related to power, cadence, speed has shown "N/A" for each parameters for around 1 second, after this time then I got the righ informations. This event accourred 2 times during the test.**

**I had the same event during last mine workout.
I left "DIRETO SIM (BLE)" trainer enabled In my trainer list of Rouvy (I belived to have changed with "DIRETO XR(ANT+)" trainer) and nRF52 switched on with FTMS_Zwift loaded, so with FTMS used as bridge. During the ride 3 N/A events accourred inside to 60 min workout window.**

> About the discrepancy between the road inclination that the training app is presenting on the screen and what that very same app is sending to the trainer (for setting is resistance) ....... we have been here before! [Please check this] (https://github.com/Berg0162/simcline/tree/master/Tacx%20Smart#simcline-in-tts4-controlled-operation)
>
> The bottom line is: **WhatYouSeeIsNotWhatYouAlwaysGet** This sometimes is due to your own settings in the App (Difficulty
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

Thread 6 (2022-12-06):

Support for other than Feather nRF52840 processors

Berg0162, 2022-12-06:
Have you considered using a D1 Mini NodeMCU ESP32 WiFi and Bluetooth BLE?
Link here: https://amzn.eu/d/2XgwXKY

ESP32 and nRF52 can do WiFi, Bluetooth Classic, and Bluetooth Low Energy (BLE), so seem are equivalent.
Are there technical limitation can't be applied to ESP32?
ESP32 is cheaper than nRF2 also low dimension

Best Regards
Filippo

_Originally posted by @cherryphilip74 in https://github.com/Berg0162/simcline/issues/5#issuecomment-1338824386_

Berg0162, 2022-12-06:
When I started the Simcline project (3 years ago),  I was looking for a processor that had ANT+ and excellent BLE support. The Adafruit support is great, with lots of code samples and a very rich library for a wide range of sensors. The Feather nRF52832 (Nordic Silicon chip) was offering the right specs. , Adafruit a quick start and steep learning curve!
Unfortunately installing the Nordic Softdevice (firmware) for ANT+ was a bridge to far for me, so I decided to go for the BLE solution and (ANT+) FE-C over BLE that is supported by TACX. At this very moment this is still working without any flaws at my home (3 times a week during indoor season). The Feather type one should buy now is a nRF52840 (more value for money) and what is more: lots of memory. The MITM implementation is at the limits of what this processor can offer due to the large throughput of the BLE channels: never miss a packet (from the trainer of Zwift) or you are down!
Later developments benefitted of the code base that I developed (after all, the cost for an IT-development project is not the processor ($24)  but the development speed of the programmer (hourly salary >$50). The FTMS enabled code development took so far more than 80 hours (!), that is low because I could reuse a lot of code from the Wahoo Sim project and the original TACX Simcline.
Yes I have been looking at other processors but a few bucks more or less is not the issue here: supplier support (installed software base), reuse of code and platform continuity are determining whether the projects are feasible and successful or not...
I am considering an ESP32 board now (Adafruit has an interesting Feather with ESP32) for future IOT projects, only because of its WIFI support. Notice that the Simcline code projects can be ported to the ESP32 platform at the cost of many hours... that I rather spent exploring new things! At the start of such an enterprise one is not sure at all, that the ESP32 is as powerful on Bluetooth, as the proven Nordic chip, when it comes to handling a heavy duty BLE MITM application!

macrocd, 2023-01-09:
I almost finish to assemble my Simcline 2.0. I Used Adafruit-ItsyBitsy-nRF52840 And SH1106 Oled display. Usually I use Rouvy+ Elite SUITO Trainer.  I'm waiting for 3D printing parts to terminate my setup.
Implementing the itsybitsy board is almost immediate. For the Display I took a little more time because I don't know the platform well.
M.

Berg0162, 2023-01-10:
Great!
Best wishes, Jörgen

Berg0162, 2023-02-13:
I have been working recently on porting the nRF52 platform Simcline code, (supporting FTMS-enabled trainers), to the ESP32 platform. I have applied an Adafruit product called Huzzah 32 ([Feather-esp32-V2](https://learn.adafruit.com/adafruit-esp32-feather-v2) to remain compatible with the Feather formfactor, to allow an easy application of the board in my Simcline 2.0 design/construction.
The process was not easy since the Adafruit/Bluefruit BLE libraries turned out to be superior over the default ESP32 Bluedroid implementation. ESP32 Bluedroid is buggy when the BLE implementation becomes more demanding than a simple single Client or single Server, as is clearly the case with BLE MITM.
Adafruit/Bluefruit on nRF52 was loaded to its limits with the FTMS supporting BLE MITM code but kept working, in the case of ESP32 Bluedroid the implementation was somewhat to demanding.... So just comparing the overal specs (on paper) of both processor platforms is not sufficient... one needs to take into account the (quality of the) available libraries as well to reach success.
Fortunately H2Zero has created a more or less compatible replacement for Bluedroid, called NimBLE [H2Zero NimBLE](https://h2zero.github.io/NimBLE-Arduino/index.html)! The application of NimBLE saved the porting project! So it looks now that we will be able to benefit of the immense specs of the ESP32 platform after all!
I will upload soon the ESP32 Simcline code for FTMS-enabled trainers and give you, ESP32 adepts, a change to test for yourself!
Best wishes,
Jörgen.

PS macrocd, how are you doing? Have you succeeded? Can you share your experience?

Berg0162, 2023-02-13:
Dear M,
Thank you for your update!
Definitely no changes with respect to the display in version 2.1. Compare and check your inserted SH1106 settings of version 011 vs 2.1...

Berg0162, 2023-02-26:
Client, Server and Bridge 1.0 versions for ESP32 platform have been uploaded now!

cherryphilip74, 2023-02-26:
I will test it tomorrowSent from Android deviceIl 26 feb 2023 11:41, Jörgen van den Berg ***@***.***> ha scritto:
Client, Server and Bridge 1.0 versions for ESP32 platform have been uploaded now!

—Reply to this email directly, view it on GitHub, or unsubscribe.You are receiving this because you were mentioned.Message ID: ***@***.***>

Berg0162, 2023-03-17:
Dear Filippo,
I am curious to hear from you about your experiences with the ESP32 code.....
Best wishes,
Jörgen.

Closed 2023-04-18.

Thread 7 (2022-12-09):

Test Zwift Hub FTMS

Berg0162, 2022-12-09:
Hello Jorghen,

Here is the first result with FTMS_Client_ v022

 I don't know if it's good?

Next test when I receive the dongle for the Pc

Friendship,
Joel

[CFG   ] SoftDevice's RAM requires: 0x20002C78
FTMS and Chars 'initialized'
CPS and Chars 'initialized'
CSCS and Chars 'initialized'
GA and Chars 'initialized'
DIS and Chars 'initialized'
Start Scanning for CPS, CSC and FTMS!
[BLE   ] BLE_GAP_EVT_ADV_REPORT : Conn Handle = 65535
[BLE   ] BLE_GAP_EVT_ADV_REPORT : Conn Handle = 65535
Found advertising Peripheral with FTMS service!, see the Raw Data packet:
Timestamp MAC Address       Rssi Data
000000681 F8:9C:FC:53:5E:49 -60  09-02-16-18-26-18-18-18-0A-18
[BLE   ] BLE_GAP_EVT_CONNECTED : Conn Handle = 0
[GAP   ] MAC = F8:9C:FC:53:5E:49, Type = 1, Resolved = 0
[GAP   ] Conn Interval = 20.00 ms, Latency = 0, Supervisor Timeout = 2000 ms
[BLE   ] BLE_GAP_EVT_DISCONNECTED : Conn Handle = 0
[GAP   ] Disconnect Reason: CONN_FAILED_TO_BE_ESTABLISHED
Feather nRF52 (Central) connected to Trainer (Peripheral) device: [] MAC Address: F8:9C:FC:53:5E:49
Now checking mandatory Client Services and Characteristics!
Discovering Client Cycling Power (CP) Service ... [DISC  ] [SVC] Handle start = 1
bool BLEDiscovery::_discoverService(uint16_t, BLEClientService&, uint16_t): 79: verify failed, error = BLE_ERROR_INVALID_CONN_HANDLE
Not Found!
Disconnecting since Client Cyling Power Service is mandatory!
Client Disconnected, reason = 0x3E
>>> Restart the Feather nRF52 Client for a new run! <<<
>>> Couldn't enable notify for Client CP Measurement Characteristic.
>>> Couldn't enable indicate for Client CP Control Point Characteristic.
>>> Couldn't enable notify for Client CSC Measurement Characteristic.
>>> Couldn't enable notify for Client FTM Training Status Characteristic.
FTMS (trainer) is controlled by another Client (Training App)!
Client (Central) is Up and Running!

BSP Library : 1.3.0
Bootloader  : s140 6.1.1
Serial No   : C2BA380FAD3CBBC2

--------- SoftDevice Config ---------
Max UUID128     : 10
ATTR Table Size : 4096
Service Changed : 1
Central Connect Setting
  - Max MTU         : 23
  - Event Length    : 3
  - HVN Queue Size  : 1
  - WrCmd Queue Size: 1

--------- BLE Settings ---------
Name            : ItsyBitsy nRF52840 Express
Max Connections : Peripheral = 0, Central = 1
Address         : E2:AA:F7:E9:06:E0 (Static)
TX Power        : 0 dBm
Conn Intervals  : min = 20.00 ms, max = 30.00 ms
Conn Timeout    : 2000 ms
Central Paired Devices:

_Originally posted by @le-joebar in https://github.com/Berg0162/simcline/issues/5#issuecomment-1342980419_

Berg0162, 2022-12-09:
Dear Joel,
Please have a look at this tool for your smartphone to help you inspecting and testing BLE devices:
[nRF Connect by Nordic](https://play.google.com/store/apps/details?id=no.nordicsemi.android.mcp&hl=en&gl=US&pli=1)
You can perfectly inspect the Zwift Hub trainer and check for the presence of BLE services like CPS, CSC, FTMS and others. You can easily connect to the trainer and test all those different Characteristics.... and their behaviour. It should be part of your toolbox I.C.E.

I have uploaded a new version for the Client (v023) that is more robust when error states occur. It will not result in an other outcome of your previous test!
Regards,
Jörgen.

le-joebar, 2022-12-09:
Hello Jorghen,

I redid the test with Ant+ disconnected and Bluethoot gsm switched off.

Here is the result with FTMS_Client_ v022:

Now I think it's  good !

Joel

PS : I'm waiting for the dongle, maybe tomorrow

Feather nRF52 Client/Central: CPS, CSC and FTMS
----------------- Version 02.2 ------------------
Initialise the Bluefruit nRF52 module: Client (Central)
[CFG   ] SoftDevice's RAM requires: 0x20002C78
FTMS and Chars 'initialized'
CPS and Chars 'initialized'
CSCS and Chars 'initialized'
GA and Chars 'initialized'
DIS and Chars 'initialized'
Start Scanning for CPS, CSC and FTMS!
Found advertising Peripheral with FTMS service!, see the Raw Data packet:
Timestamp MAC Address       Rssi Data
000016641 F8:9C:FC:53:5E:49 -68  09-02-16-18-26-18-18-18-0A-18
[BLE   ] BLE_GAP_EVT_CONNECTED : Conn Handle = 0
[GAP   ] MAC = F8:9C:FC:53:5E:49, Type = 1, Resolved = 0
[GAP   ] Conn Interval = 20.00 ms, Latency = 0, Supervisor Timeout = 2000 ms
[BLE   ] BLE_GATTS_EVT_EXCHANGE_MTU_REQUEST : Conn Handle = 0
[GAP   ] ATT MTU is changed to 23
[BLE   ] BLE_GAP_EVT_DATA_LENGTH_UPDATE_REQUEST : Conn Handle = 0
[GAP   ] Data Length Request is (tx, rx) octets = (251, 251), (tx, rx) time = (2120, 2120) us
[BLE   ] BLE_GAP_EVT_DATA_LENGTH_UPDATE : Conn Handle = 0
[GAP   ] Data Length is (tx, rx) octets = (27, 27), (tx, rx) time = (1370, 1370) us
[BLE   ] BLE_GATTC_EVT_CHAR_VAL_BY_UUID_READ_RSP : Conn Handle = 0
Feather nRF52 (Central) connected to Trainer (Peripheral) device: [Zwift Hub] MAC Address: F8:9C:FC:53:5E:49
Now checking mandatory Client Services and Characteristics!
Discovering Client Cycling Power (CP) Service ... [DISC  ] [SVC] Handle start = 1
[BLE   ] BLE_GATTC_EVT_PRIM_SRVC_DISC_RSP : Conn Handle = 0
[DISC  ] [SVC] Service Count: 1
[DISC  ] [SVC] Found 0x1818, Handle start = 41, end = 48
-----------------
Found it! CPS Max Payload: 20 Data Length: 27
Discovering Client CP Measurement characteristic ... [DISC  ] [CHR] Handle start = 41, end = 48
[BLE   ] BLE_GATTC_EVT_CHAR_DISC_RSP : Conn Handle = 0
[DISC  ] [CHR] Characteristic Count: 3
[DISC  ] [CHR] Found 0x2A63, handle = 43
-----------------
[DISC  ] [DESC] Handle start = 44, end = 48
[BLE   ] BLE_GATTC_EVT_DESC_DISC_RSP : Conn Handle = 0
[DISC  ] [DESC] Descriptor Count: 5
[DISC  ] [DESC] Descriptor 0: uuid = 0x2902, handle = 44
[DISC  ] [DESC] Descriptor 1: uuid = 0x2803, handle = 45
[DISC  ] [DESC] Descriptor 2: uuid = 0x2A65, handle = 46
[DISC  ] [DESC] Descriptor 3: uuid = 0x2803, handle = 47
[DISC  ] [DESC] Descriptor 4: uuid = 0x2A5D, handle = 48
[DISC  ] Found CCCD: handle = 44
Found it!
Discovering Client CP Control Point characteristic ... [DISC  ] [CHR] Handle start = 41, end = 48
[BLE   ] BLE_GATTC_EVT_CHAR_DISC_RSP : Conn Handle = 0
[DISC  ] [CHR] Characteristic Count: 3
[DISC  ] [CHR] Handle start = 49, end = 48
[BLE   ] BLE_GATTC_EVT_CHAR_DISC_RSP : Conn Handle = 0
[DISC  ] [CHR] Characteristic Count: 0
[DISC  ] [CHR] Gatt Status = 0x0101
Not Found! NOT Mandatory!
Discovering Client CP Feature characteristic ... [DISC  ] [CHR] Handle start = 41, end = 48
[BLE   ] BLE_GATTC_EVT_CHAR_DISC_RSP : Conn Handle = 0
[DISC  ] [CHR] Characteristic Count: 3
[DISC  ] [CHR] Found 0x2A65, handle = 46
-----------------
Found it!
[BLE   ] BLE_GATTC_EVT_READ_RSP : Conn Handle = 0
 -> Client Reads Raw CP Feature bytes: [4] [ 0C 00 00 00 ]
Wheel revolution data supported
Crank revolution data supported
Discovering Client CP Sensor Location characteristic ... [DISC  ] [CHR] Handle start = 41, end = 48
[BLE   ] BLE_GATTC_EVT_CHAR_DISC_RSP : Conn Handle = 0
[DISC  ] [CHR] Characteristic Count: 3
[DISC  ] [CHR] Found 0x2A5D, handle = 48
-----------------
Found it!
 -> Client Reads CP Location Sensor: Loc#: 0 Other
Discovering Cycling Speed and Cadence (CSC) Service ... [DISC  ] [SVC] Handle start = 1
bool BLEDiscovery::_discoverService(uint16_t, BLEClientService&, uint16_t): 79: verify failed, error = NRF_ERROR_BUSY
Not Found and disconnecting!
CSC Service is mandatory!
[BLE   ] BLE_GATTC_EVT_READ_RSP : Conn Handle = 0
[BLE   ] BLE_GAP_EVT_DISCONNECTED : Conn Handle = 0
[GAP   ] Disconnect Reason: LOCAL_HOST_TERMINATED_CONNECTION
Client Disconnected, reason = 0x16
>>> Restart the Feather nRF52 Client for a new run! <<<
>>> Couldn't enable notify for Client CP Measurement Characteristic.
>>> Couldn't enable indicate for Client CP Control Point Characteristic.
>>> Couldn't enable notify for Client CSC Measurement Characteristic.
>>> Couldn't enable notify for Client FTM Training Status Characteristic.
FTMS (trainer) is controlled by another Client (Training App)!
Client (Central) is Up and Running!

BSP Library : 1.3.0
Bootloader  : s140 6.1.1
Serial No   : C2BA380FAD3CBBC2

--------- SoftDevice Config ---------
Max UUID128     : 10
ATTR Table Size : 4096
Service Changed : 1
Central Connect Setting
  - Max MTU         : 23
  - Event Length    : 3
  - HVN Queue Size  : 1
  - WrCmd Queue Size: 1
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
le-joebar, 2022-12-10:
I don't know if this can't help you?  :
Conect nrf debug mode log

nRF Connect, 2022-12-10
Zwift Hub (F8:9C:FC:53:5E:49)
V 16:01:11.439 Connecting to F8:9C:FC:53:5E:49...
D 16:01:11.439 gatt = device.connectGatt(autoConnect = false, TRANSPORT_LE, preferred PHY = LE 1M)
D 16:01:11.697 [Callback] Connection state changed with status: 0 and new state: CONNECTED (2)
I 16:01:11.697 Connected to F8:9C:FC:53:5E:49
V 16:01:11.702 Discovering services...
D 16:01:11.702 gatt.discoverServices()
D 16:01:11.728 [Broadcast] Action received: android.bluetooth.device.action.ACL_CONNECTED
I 16:01:12.541 Connection parameters updated (interval: 7.5ms, latency: 0, timeout: 5000ms)
D 16:01:15.576 [Callback] Services discovered with status: 0
I 16:01:15.577 Services discovered
V 16:01:15.615 Generic Access (0x1800)
- Device Name [R W] (0x2A00)
- Appearance [R] (0x2A01)
- Peripheral Preferred Connection Parameters [R] (0x2A04)
- Central Address Resolution [R] (0x2AA6)
Generic Attribute (0x1801)
- Service Changed [I] (0x2A05)
   Client Characteristic Configuration (0x2902)
Fitness Machine (0x1826)
- Indoor Bike Data [N] (0x2AD2)
   Client Characteristic Configuration (0x2902)
- Fitness Machine Feature [R] (0x2ACC)
- Supported Resistance Level Range [R] (0x2AD6)
- Supported Power Range [R] (0x2AD8)
- Fitness Machine Status [N] (0x2ADA)
   Client Characteristic Configuration (0x2902)
- Fitness Machine Control Point [I W] (0x2AD9)
   Client Characteristic Configuration (0x2902)
Cycling Speed and Cadence (0x1816)
- CSC Measurement [N] (0x2A5B)
   Client Characteristic Configuration (0x2902)
- CSC Feature [R] (0x2A5C)
- Sensor Location [R] (0x2A5D)
- SC Control Point [I W] (0x2A55)
   Client Characteristic Configuration (0x2902)
Cycling Power (0x1818)
- Cycling Power Measurement [N] (0x2A63)
   Client Characteristic Configuration (0x2902)
- Cycling Power Feature [R] (0x2A65)
- Sensor Location [R] (0x2A5D)
Secure DFU Service (0xFE59)
- Buttonless DFU [I W] (8ec90003-f315-4f60-9fb8-838830daea50)
   Client Characteristic Configuration (0x2902)
Heart Rate (0x180D)
- Heart Rate Measurement [N] (0x2A37)
   Client Characteristic Configuration (0x2902)
- Body Sensor Location [R] (0x2A38)
Unknown Service (c4630001-003f-4cec-8994-e489b04d857f)
- Unknown Characteristic [R] (c4632b03-003f-4cec-8994-e489b04d857f)
- Unknown Characteristic [N R] (c4632b05-003f-4cec-8994-e489b04d857f)
   Client Characteristic Configuration (0x2902)
   Characteristic User Description (0x2901)
- Unknown Characteristic [I W] (c4632b04-003f-4cec-8994-e489b04d857f)
   Client Characteristic Configuration (0x2902)
Device Information (0x180A)
- Manufacturer Name String [R] (0x2A29)
- Model Number String [R] (0x2A24)
- Serial Number String [R] (0x2A25)
- Hardware Revision String [R] (0x2A27)
- Firmware Revision String [R] (0x2A26)
D 16:01:15.616 gatt.setCharacteristicNotification(00002a05-0000-1000-8000-00805f9b34fb, true)
D 16:01:15.621 gatt.setCharacteristicNotification(00002ad2-0000-1000-8000-00805f9b34fb, true)
D 16:01:15.624 gatt.setCharacteristicNotification(00002ada-0000-1000-8000-00805f9b34fb, true)
D 16:01:15.627 gatt.setCharacteristicNotification(00002ad9-0000-1000-8000-00805f9b34fb, true)
D 16:01:15.630 gatt.setCharacteristicNotification(00002a5b-0000-1000-8000-00805f9b34fb, true)
D 16:01:15.632 gatt.setCharacteristicNotification(00002a55-0000-1000-8000-00805f9b34fb, true)
D 16:01:15.635 gatt.setCharacteristicNotification(00002a63-0000-1000-8000-00805f9b34fb, true)
D 16:01:15.637 gatt.setCharacteristicNotification(00002a37-0000-1000-8000-00805f9b34fb, true)
D 16:01:15.640 gatt.setCharacteristicNotification(c4632b05-003f-4cec-8994-e489b04d857f, true)
D 16:01:15.643
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

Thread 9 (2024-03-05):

FTMS_client code with Jetblack volt trainer using ESP-wroom-32

davidbonenfant52, 2024-03-05:
Hi berg0162,
I get "Client Reads HR Location Sensor:Guru Meditation Error: Core  1 panic'ed (LoadProhibited). Exception was unhandled." error when I try to run the ftms_client code. I have pasted the serial monitor output below of the full cycle everytime the board reboots. I also tried the FTMS_server code and it works just fine. Let me know if you need more information to find out why it is not working with my particular set up. Thank you in advance.

 -> Client Reads Device Name:   [Volt]
 -> Client Reads Appearance:    [1152]
Client Device Information Service: Found!
 -> Client Reads Manufacturer Name: [JetBlack]
 -> Client Reads Model Number:      [05]
 -> Client Reads Serial Number:     [828]
Client_CyclingPower_Service: Found!
Client_CP_Measurement_Chr: Found!
Client_CP_Feature_Chr: Found!
 -> Client Reads Raw CP Feature bytes: [4] [ 0C 00 00 00 ]
Wheel revolution data supported
Crank revolution data supported
Client_CP_Location_Chr: Found!
 -> Client Reads HR Location Sensor:Guru Meditation Error: Core  1 panic'ed (LoadProhibited). Exception was unhandled.

Core  1 register dump:
PC      : 0x4009140c  PS      : 0x00060c30  A0      : 0x8011ae48  A1      : 0x3ffc85d0
A2      : 0xff00ffff  A3      : 0xff00fffb  A4      : 0x000000ff  A5      : 0x0000ff00
A6      : 0x00ff0000  A7      : 0xff000000  A8      : 0x00000000  A9      : 0x3ffc8a06
A10     : 0x3ffc8a03  A11     : 0x3ffc87d1  A12     : 0x00000003  A13     : 0x00000001
A14     : 0x00060e20  A15     : 0x00000001  SAR     : 0x00000004  EXCCAUSE: 0x0000001c
EXCVADDR: 0xff00ffff  LBEG    : 0x4009142d  LEND    : 0x4009143d  LCOUNT  : 0xffffffff

Backtrace: 0x40091409:0x3ffc85d0 0x4011ae45:0x3ffc85e0 0x40121e7a:0x3ffc88f0 0x40121eb6:0x3ffc8980 0x400e6e46:0x3ffc89c0 0x400d25fa:0x3ffc8a60 0x400d34fc:0x3ffc8ab0 0x400d3552:0x3ffc8ad0 0x400e7ab9:0x3ffc8b10

ELF file SHA256: 22369bb919dc67f3

Rebooting...
ets Jun  8 2016 00:22:57

rst:0xc (SW_CPU_RESET),boot:0x13 (SPI_FAST_FLASH_BOOT)
configsip: 0, SPIWP:0xee
clk_drv:0x00,q_drv:0x00,d_drv:0x00,cs0_drv:0x00,hd_drv:0x00,wp_drv:0x00
mode:DIO, clock div:1
load:0x3fff0030,len:1344
load:0x40078000,len:13964
load:0x40080400,len:3600
entry 0x400805f0
  ESP32 BLE Client/Central: CPS, CSC, HBM and FTMS
------------------- Version 01.0 --------------------
Client Starts Scanning for Server Device with CPS, CSC and FTMS!
BLE Advertised Device found: Name: , Address: 52:13:3e:f4:ba:09, manufacturer data: 4c001005231828fa3f, txPower: 7
BLE Advertised Device found: Name: , Address: 40:a0:23:a6:b2:78, manufacturer data: 4c001005171857574b, txPower: 11
BLE Advertised Device found: Name: Volt, Address: ed:84:37:e2:f5:e5, appearance: 1152, serviceUUID: 0x1826
Service Data:
UUID: 0x1826, Data:
Client Connection Parameters -> Interval: [40] Latency: [0] Supervision Timeout: [256]
ESP32 Client connected to Server device with Name: [Volt] MAC Address: [ED:84:37:E2:F5:E5] MTU: [244]
Now checking all Client Services and Characteristics!
If Mandatory Services Fail --> the Client will disconnect!
Client Generic Access: Found!
 -> Client Reads Device Name:   [Volt]
 -> Client Reads Appearance:    [1152]

Berg0162, 2024-03-06:
Dear David,
An ESP32 Guru in panic .... that is not what one wants to experience!
Are the Jetblack Volt Trainer engineers not the same ones behind the Zwift Hub? The last one is known to work perfectly with the very same code (client, bridge and Simcline). Apparently the engineers have made a crucial change in the code for the Jetblack  Volt that made the ESP32 Guru panic. I am not sure what exactly has been changed but I have published a Client v012 that is more robust when reading the sensor locations of CPS, CSC and HBM. The panic occurred with CP but I assumed CSC and HBM would face the same problem when it was their turn.... Please keep me posted!
Best wishes,
Jörgen.

davidbonenfant52, 2024-03-07:
Hi Jorgen
Thanks for the quick reply.
From what I've read it seems the zwift and volt trainers have indepedent software teams but may be collaborating given the physical trainer is pretty much the same.
I have tried the Client v012 and it seems to be working! I am getting ongoing readings from the trainer for resistance level, instantaneous power, average power etc. so looks good.
I have yet to try the bridge but I'm guessing it will require the modification that you did for the client code?

Berg0162, 2024-03-07:
Good morning David,
It is always nice to take the panic away! I will modify all the programs accordingly a.s.a.p. and upload new versions! Check the repository and continue your reconnaissance. However, I am still very curious to see what the serial monitor output is exactly telling us, now that the Client is working without failure. I want to know what these engineers have changed when reading the sensor locations, that caused the fatal failure. I have sticked (as far as I know) to what is published by the standard committee that oversees FTMS...
Please copy/paste the (relevant) output when running the code again, I would very much appreciate that!
Best wishes,
Jörgen.

davidbonenfant52, 2024-03-08:
Hi again Jorgen,

This time it is not a panic issue but a resistance issue!

Sorry but I may have jumped to conclusions while testing the client code. The esp32 is picking up the trainer data but it is not simulating changes in resistance. I also tried the bridge code and it is functioning in transmitting trainer data to app but the app doesn't seem to be transmitting resistance to the trainer. I posted the serial monitor output for the client code here (and afterwards for the bridge code):

ets Jun  8 2016 00:22:57

rst:0x1 (POWERON_RESET),boot:0x13 (SPI_FAST_FLASH_BOOT)
configsip: 0, SPIWP:0xee
clk_drv:0x00,q_drv:0x00,d_drv:0x00,cs0_drv:0x00,hd_drv:0x00,wp_drv:0x00
mode:DIO, clock div:1
load:0x3fff0030,len:1344
load:0x40078000,len:13964
load:0x40080400,len:3600
entry 0x400805f0
  ESP32 BLE Client/Central: CPS, CSC, HBM and FTMS
------------------- Version 01.2 --------------------
Client Starts Scanning for Server Device with CPS, CSC and FTMS!
BLE Advertised Device found: Name: , Address: 5a:be:ec:49:ea:07, manufacturer data: 0600010920020bd959614b10c95494ffa2455706e96d368ec53cd0c56a
BLE Advertised Device found: Name: , Address: 33:cf:94:8b:19:5f, manufacturer data: 060001092022f419e6d1a828f86633a146020d97e97704450f0f51edd4
BLE Advertised Device found: Name: , Address: 08:59:45:e2:c1:5d, manufacturer data: 06000109202291984ada6d2d4cff4187a8e61b664699faaae5988715a6
BLE Advertised Device found: Name: Volt, Address: ed:84:37:e2:f5:e5, appearance: 1152, serviceUUID: 0x1826
Service Data:
UUID: 0x1826, Data:
Client Connection Parameters -> Interval: [40] Latency: [0] Supervision Timeout: [256]
ESP32 Client connected to Server device with Name: [Volt] MAC Address: [ED:84:37:E2:F5:E5] MTU: [244]
Now checking all Client Services and Characteristics!
If Mandatory Services Fail --> the Client will disconnect!
Client Generic Access: Found!
 -> Client Reads Device Name:   [Volt]
 -> Client Reads Appearance:    [1152]
Client Device Information Service: Found!
 -> Client Reads Manufacturer Name: [JetBlack]
 -> Client Reads Model Number:      [05]
 -> Client Reads Serial Number:     [828]
Client_CyclingPower_Service: Found!
Client_CP_Measurement_Chr: Found!
Client_CP_Feature_Chr: Found!
 -> Client Reads Raw CP Feature bytes: [4] [ 0C 00 00 00 ]
Wheel revolution data supported
Crank revolution data supported
Client_CP_Location_Chr: Found!
 -> Client Reads CP Location Sensor: Loc#: 201
Cycling Power Measurement: Notify Enabled!
Client_CyclingSpeedCadence_Service: Found!
Client_CSC_Measurement_Chr: Found!
Client_CSC_Feature_Chr: Found!
 -> Client Reads Raw CSC Feature bytes: [2] [ 03 00 ]
Wheel rev supported
Crank rev supported
Client_CSC_Location_Chr: Found!
 -> Client Reads CSC Location Sensor: Loc#: 12 Rear wheel
Client_CSC_Measurement_Chr: Notify Enabled!
Client_FitnessMachine_Service: Found!
Client_FTM_Feature_Chr: Found!
 -> Client Reads Raw FTM Feature bytes: [8] [ 87 44 00 00 0C E0 00 00 ]
- Fitness Machine Features:
Average Speed Supported
Cadence Supported
Total Distance Supported
Resistance Level Supported
Heart Rate Measurement Supported
Power Measurement Supported
- Target Setting Features:
Resistance Target Setting Supported
Power Target Setting Supported
Indoor Bike Simulation Parameters Supported
Wheel Circumference Configuration Supported
Spin Down Control Supported
Client_FTM_IndoorBikeData_Chr: Found!
Client_FTM_IndoorBikeData_Chr: Notify Enabled!
 -> Client Rec'd Raw FTM Indoor Bike Data: [1] [11] [ 64 02 00 00 00 00 14 00 00 00 00 ]
Instant. Speed: 0 KPH Instantaneous Cadence: 0 RPM Resistance Level: 20  Instantaneous Power: 0 Watt Heart Rate: 0 HBM
 -> Client Rec'd Raw FTM Indoor Bike Data: [1] [11] [ 64 02 00 00 00 00 14 00 00 00 00 ]
Instant. Speed: 0 KPH Instantaneous Cadence: 0 RPM Resistance Level: 20  Instantaneous Power: 0 Watt Heart Rate: 0 HBM
 -> Client Rec'd Raw FTM Indoor Bike Data: [1] [11] [ 64 02 00 00 00 00 14 00 00 00 00 ]
Instant. Speed: 0 KPH Instantaneous Cadence: 0 RPM Resistance Level: 20  Instantaneous Power: 0 Watt Heart Rate: 0 HBM
 -> Client Rec'd Raw FTM Indoor Bike Data: [1] [11] [ 64 02 00 00 00 00 14 00 00 00 00 ]
Instant. Speed: 0 KPH Instantaneous Cadence: 0 RPM Resistance Level: 20  Instantaneous Power: 0 Watt Heart Rate: 0 HBM
 -> Client Rec'd Raw FTM Indoor Bike Data: [1] [11] [ 64 02 00 00 00 00 14 00 00 00 00 ]
Instant. Speed: 0 KPH Instantaneous Cadence: 0 RPM Resistance Level: 20  Instantaneous Power: 0 Watt Heart Rate: 0 HBM
 -> Client Rec'd Raw FTM Indoor Bike Data: [1] [11] [ 64 02 00 00 00 00 14 00 00 00 00 ]
Instant. Speed: 0 KPH Instantaneous Cadence: 0 RPM Resistance Level: 20  Instantaneous Power: 0 Watt Heart Rate: 0 HBM
 -> Client Rec'd Raw FTM Indoor Bike Data: [1] [11] [ 64 02 00 00 00 00 14 00 00 00 00 ]
Instant. Speed: 0 KPH Instantaneous Cadence: 0 RPM Resistance Level: 20  Instantaneous Power: 0 Watt Heart Rate: 0 HBM
 -> Client Rec'd Raw FTM Indoor Bike Data: [1] [11] [ 64 02 00 00 00 00 14 00 00 00 00 ]
Client_FTM_TrainingStatus_Chr: Not Found!
 -> Client Rec'd Raw FTM Indoor Bike Data: [1] [11] [ 64 02 00 00 00 00 14 00 00 00 00 ]
Instant. Speed: 0 KPH Instantaneous Cadence: 0 RPM Resistance Level: 20  Instantaneous Power: 0 Watt Heart Rate: 0 HBM
 -> Client Rec'd Raw FTM Indoor Bike Data: [1] [11] [ 64 02 00 00 00 00 14 00 00 00 00 ]
Instant. Speed: 0 KPH Instantaneous Cadence: 0 RPM Resistance Level: 20  Instantaneous Power: 0 Watt Heart Rate: 0 HBM
 -> Client Rec'd Raw FTM Indoor Bike Data: [1] [11] [ 64 02 00 00 00 00 14 00 00 00 00 ]
Instant. Speed: 0 KPH Instantaneous Cadence: 0 RPM Resistance Level: 20  Instantaneous Power: 0 Watt Heart Rate: 0 HBM
 -> Client Rec'd Raw FTM Indoor Bike Data: [1] [11] [ 64 02 00 00 00 00 14 00 00 00 00 ]
Instant. Speed: 0 KPH Instantaneous Cadence: 0 RPM Resistance Level: 20  Instantaneous Power: 0 Watt Heart Rate: 0 HBM
 -> Client Rec'd Raw FTM Indoor Bike Data: [1] [11] [ 64 02 00 00 00 00 14 00 00 00 00 ]
Instant. Speed: 0 KPH Instantaneous Cadence: 0 RPM Resistance Level: 20  Instantaneous Power: 0 Watt Heart Rate: 0 HBM
 -> Client Rec'd Raw FTM Indoor Bike Data: [1] [11] [ 64 02 00 00 00 00 14 00 00 00 00 ]
Instant. Speed: 0 KPH Instantaneous Cadence: 0 RPM Resistance Level: 20  Instantaneous Power: 0 Watt Heart Rate: 0 HBM
Client_FTM_SupportedResistanceLevelRange_Chr: Found!
 -> Client Rec'd Raw FTM Indoor Bike Data: [1] [11] [ 64 02 00 00 00 00 14 00 00 00 00 ]
Instant. Speed: 0 KPH Instantaneous Cadence: 0 RPM Resistance Level: 20  Instantaneous Power: 0 Watt Heart Rate: 0 HBM
 -> Client Rec'd Raw FTM Indoor Bike Data: [1] [11] [ 64 02 00 00 00 00 14 00 00 00 00 ]
Instant. Speed: 0 KPH Instantaneous Cadence: 0 RPM Resistance Level: 20  Instantaneous Power: 0 Watt Heart Rate: 0 HBM
 -> Client Rec'd Raw FTM Indoor Bike Data: [1] [11] [ 64 02 00 00 00 00 14 00 00 00 00 ]
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

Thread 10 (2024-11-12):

Zwift Trainer Dificulty

acwalter, 2024-11-12:
Zwift trainer difficulty, by default set to 50%, causes Zwift to send the grade *.5 so the simcline only receives 1/2 the actual grade. Do others experience this? My quick fix is to set the GradeChangeFactor to 200.

If this is they way Zwift works, I though I would use the .aia file in the MIT app builder and update the incline slider to allow values from 0-200, maybe even 400 if someone were to use Zwift at 25% trainer dificulty, instead of 0-100. The only trouble I am having is getting the apk to run on my phone. If I import a project and use the latest 2.5.1.aia file, and then generate an apk without changing anything I get an error when connecting to the simcline. Anyone know if there is something additional I need to do other than import the .aia file?

Berg0162, 2024-11-14:
Dear Walter,
>Zwift trainer difficulty, by default set to 50%, causes Zwift to send the grade *.5 so the simcline omly receives 1/2 the actual grade. Do others experience this? My quick fix is to set the GradeChangeFactor to 200.<br>

The trainer calculates the resistance, among others using the road grade information. That's why Zwift sends modified road grades to the trainer, dependent of the difficulty setting. Just for the record, when you change the Zwift difficulty setting from 50% to 100%, Zwift will send genuine (i.e. unmodified) grades to the trainer (WYSIWYG) and as a consequence the Simcline will lift accordingly! That is really a quick fix! The Zwifters I know, have all the Zwift difficulty setting at 100%, because they want a "road-realistic" experience when training and racing indoors with Zwift.<br>

The GradeChangeFactor functionality was originally designed and implemented to allow the Simcline user to attenuate the actuator movements not the opposite! Feel free to modify the code to whatever conforms your preferences.<br>

>and then generate an apk wothout chabging anything I get an error when connecting to the simcline<br>

It would help when you document the error state that you encounter....

Berg0162, 2024-11-24:
Issue seems to be fixed!

acwalter, 2025-01-01:
I finally had time to look into this and found the issue with the BLE extension causing crashes on my version of Android. It has a patch https://iot.appinventor.mit.edu/iot/reference/bluetoothle

Closed 2024-11-24.

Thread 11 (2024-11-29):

V12 won't connect Kickr Core on bluetooth

Fukkie-S, 2024-11-29:
Hi Jörgen,

As you mentioned to open an issue on Github, here is my loaded V12 program and the serial monitor output (after reset). Hope you can find why SIM32 won't connect Kickr anymore. I tried V11 and this version fix my Kickr immidiately.

And sorry for my English, my 4y education on the lower technical school is 45 year ago :-)

Best regards

Jan-Willem

Fukkie-S, 2024-11-29:
```cpp
/*********************************************************************
 This is programming code for ESP32 Espressif Wroom boards

      Tested with Adafruit Feather ESP32 V2 a.k.a. Huzzah

 The code uses heavily the supplied ESP32 NimBLE libraries !!  
      see: https://github.com/h2zero/NimBLE-Arduino
 Many have invested time and resources providing open source code!

        MIT license, check LICENSE for more information
        All text must be included in any redistribution
*********************************************************************/

/* -----------------------------------------------------------------------------------------------------
 *             This code should work with all indoor cycling trainers that fully support,
 *              Wahoo Kickr, Cycling Power Service and Cycling Speed & Cadence Service
 * ------------------------------------------------------------------------------------------------------
 *
 *  The code links a BLE Server (a peripheral to Zwift) and a BLE Client (a central to the Trainer) with a bridge
 *  in between, the ESP32 being man-in-the-middle (MITM). The ESP32 is an integral part of the Simcline,
 *  that interprets the exchanged road grade and moves the front wheel up and down with the change in inclination.
 *  The ESP32-bridge can control, filter and alter the bi-directional interchanged data!
 *  The client-side (central) scans and connects with the trainer relevant services: CPS + Wahoo and CSC (optional).
 *  It collects all cyling data of the services and passes these on to the server-side....
 *  The client-side supplies the indoor trainer with target and resistance control data.
 *  The server-side (peripheral) advertises and enables connection with cycling apps like Zwift and collects the app's
 *  control commands, target and resistance data. It passes these on to the client-side....
 *  The server-side supplies the app with the generated cycling data in return.
 *
 *  The client plus server (MITM) are transparent to the Wahoo trainer as well as to the training app Zwift or alike!
 *
 *  Requirements: Zwift app or alike, operational Simcline and a Wahoo Kickr trainer
 *  0) Upload and Run this code on the Simcline (i.c. ESP32 board)
 *  1) Start the Serial Monitor to catch debugging info and check the Oled display
 *  2) The code will do basic testing of mechanical parts and sensors
 *  3) Start/Power On the indoor trainer
 *  4) Simcline and trainer (with <name>) will pair as reported in the output
 *  5) Start Zwift on your computer or tablet and wait....
 *  6) Search on the Zwift pairing screens for the Simcline a.k.a. <SIM32>
 *  7) Pair: Power, Cadence and Controllable one after another with <SIM32>
 *  8) Optionally one can pair as well devices for heartrate and/or steering (Sterzo)
 *  9) Start the default Zwift ride or any ride you wish
 * 10) Make Serial Monitor output window visible on top of the Zwift window
 * 11) Hop on the bike: do the work and feel resistance change with the road
 * 12) Inspect the info presented by Serial Monitor.....
 *
 *  This device is identified with the name <SIM32>. You will see this only when connecting to Zwift on the
 *  pairing screens! Notice: Zwift extends device names with additional numbers for identification!
 *
 */

/*
Version 1.0
Changed Stack Depth values from 2048 to 4096 for Server Control Point Indicate (modified) and Write w Response
Version 1.1
Inserted check (boolean) on Control Point Write-Response out of synch...
Version 1.2
Changed device identification naming to a simpler scheme: SIM32 or SIM52 instead of <SIM DevName>
Server Characteristic values (read only) are now updated when a new client connection is established
NimBLE registerForNotify() has been deprecated and is replaced with subscribe() / unsubscribe()
*/

// -------------------------------------------------------------------------------------------
// COMPILER DIRECTIVE to allow/suppress DEBUG messages that help debugging...
// Uncomment general "#define DEBUG" to activate
#define DEBUG
// Include these debug utility macros in all cases!
#include "DebugUtils.h"
#ifdef DEBUG
//  Restrict activating one or more of the following DEBUG directives --> process intensive
//  The overhead can lead to spurious side effects and a loss of quality of service handling!!
//#define DEBUG_CP_MEASUREMENT    // If defined allows for parsing and decoding the Cycling Power Data
//#define DEBUG_CSC_MEASUREMENT   // If defined allows for parsing and decoding the Cycling Speed and Cadence Data
//#define DEBUG_WAHOO_CONTROLPOINT_RESPONSE     // If defined allows for parsing the Data
//#define DEBUG_WAHOO_CONTROLPOINT_OPCODE_DATA  // If defined allows for parsing and decoding Data
//#define MOVEMENTDEBUG
#endif
// --------------------------------------------------------------------------------------------
#ifndef ADAFRUIT_FEATHER_ESP32_V2
#define ADAFRUIT_FEATHER_ESP32_V2
#endif

// Exponential EMA ALPHA filter definition
// Used to filter sequence of actuator target positions --> minimize consecutive small up/down movements
// Should be between low (10-40) is maximal and high (50-90) is minimal filtering
// Uncomment "#define EMA_ALPHA" to activate
//#define EMA_ALPHA 60    // Value is in percentage 0-99.

#define 	BLE_APPEARANCE_GENERIC_CYCLING   1152

#include <NimBLEDevice.h>
// We need this for setting the Server-side Generic Access Char's --> Appearance and DeviceName
#include <nimble/nimble/host/services/gap/include/services/gap/ble_svc_gap.h>

#define THISDEVICENAME "SIM32" // Shortname

const uint8_t MAX_PAYLOAD = 20; // Max 20 byte data size for single packet BLE transfer

// Struct containing Device info to administer dis/connected devices
typedef struct
{
  uint8_t PeerAddress[6];
  std::string PeerName;
  uint16_t conn_handle;
  bool IsConnected;
} Device_info_t;
// -----------------------------------------------------------------
// Your hardware MAC/DEVICE ADDRESSES
// Laptop/Desktop Device Address that runs Zwift, in printed format: [00:01:02:03:04:05]
// NimBLE demands you to enter addresses here in Little Endian format (reversed order)
#define LAPTOPADDRESS {0xbc,0xa0,0xec,0x7b,0x57,0xd0} // Little Endian format!!
// Trainer Wahoo Device Address, in printed format: [00:01:02:03:04:05]
#define TRAINERADDRESS {0xcf,0xc4,0x8c,0x1a,0x39,0xe5} // Little Endian format!!
// -----------------------------------------------------------------
// Initialize connectable device registration
Device_info_t Trainer    = {TRAINERADDRESS, "MyTrainer", BLE_HS_CONN_HANDLE_NONE, false};
Device_info_t Laptop     = { LAPTOPADDRESS, "MyLaptop" , BLE_HS_CONN_HANDLE_NONE, false};
Device_info_t Smartphone = {        {0x00}, "MyPhone"  , BLE_HS_CONN_HANDLE_NONE, false};
// ----------------------------------------------------------------------------------

// Client Generic Access --------------------------------------------------------------
#define UUID16_SVC_GENERIC_ACCESS                             BLEUUID((uint16_t)0x1800)
#define UUID16_CHR_DEVICE_NAME                                BLEUUID((uint16_t)0x2A00)
#define UUID16_CHR_APPEARANCE                                 BLEUUID((uint16_t)0x2A01)
#define UUID16_CHR_PERIPHERAL_PREFERRED_CONNECTION_PARAMETERS BLEUUID((uint16_t)0x2A04)
#define UUID16_CHR_CENTRAL_ADDRESS_RESOLUTION                 BLEUUID((uint16_t)0x2AA6)
BLERemoteService* pRemote_GenericAccess_Service;
BLERemoteCharacteristic* pRemote_GA_Appearance_Chr; // Read
uint16_t client_GA_Appearance_Value = BLE_APPEARANCE_GENERIC_CYCLING;  // Default decimal: 1152 -> Generic Cycling
BLERemoteCharacteristic* pRemote_GA_DeviceName_Chr;// Read, Write
std::string client_GA_DeviceName_Str = THISDEVICENAME;

// Client Service Device Information --------------------------------------------------
#define UUID16_SVC_DEVICE_INFORMATION                         BLEUUID((uint16_t)0x180A)
#define UUID16_CHR_MODEL_NUMBER_STRING                        BLEUUID((uint16_t)0x2A24)
#define UUID16_CHR_SERIAL_NUMBER_STRING                       BLEUUID((uint16_t)0x2A25)
#define UUID16_CHR_MANUFACTURER_NAME_STRING                   BLEUUID((uint16_t)0x2A29)
/*
#define UUID16_CHR_FIRMWARE_REVISION_STRING                   BLEUUID((uint16_t)0x2A26)
#define UUID16_CHR_HARDWARE_REVISION_STRING                   BLEUUID((uint16_t)0x2A27)
#define UUID16_CHR_SOFTWARE_REVISION_STRING                   BLEUUID((uint16_t)0x2A28)
*/
BLERemoteService*  pRemote_DeviceInformation_Service;
BLERemoteCharacteristic* pRemote_DIS_ManufacturerName_Chr;   // Read
std::string client_DIS_Manufacturer_Str;
BLERemoteCharacteristic* pRemote_DIS_ModelNumber_Chr;       // Read
std::string client_DIS_ModelNumber_Str;
BLERemoteCharacteristic* pRemote_DIS_SerialNumber_Chr;      // Read
std::string client_DIS_SerialNumber_Str;
// -------------------------------------------------------------------------------------
BLEService *server_DeviceInformation_Service;
BLECharacteristic *server_DIS_ModelNumber_Chr;       // Read
BLECharacteristic *server_DIS_SerialNumber_Chr;      // Read
BLECharacteristic *server_DIS_ManufacturerName_Chr;  // Read
/*
BLECharacteristic *server_DIS_Firmware_Chr;          // Read
std::string client_DIS_Firmware_Str = "12345";
BLECharacteristic *server_DIS_Hardware_Chr;          // Read
std::string client_DIS_Hardware_Str = "12345";
BLECharacteristic *server_DIS_Software_Chr;          // Read
std::string client_DIS_Software_Str = "12345";
*/
//--------------------------------------------------------------------------------------

/* NORDIC UART SERVICE a.k.a. NUS
 * NUS Service: 6E400001-B5A3-F393-E0A9-E50E24DCCA9E
 * NUS RXD    : 6E400002-B5A3-F393-E0A9-E50E24DCCA9E
 * NUS TXD    : 6E400003-B5A3-F393-E0A9-E50E24DCCA9E
 */
BLEUUID UUID_NUS_SERVICE("6E400001-B5A3-F393-E0A9-E50E24DCCA9E");
BLEUUID UUID_NUS_CHR_RXD("6E400002-B5A3-F393-E0A9-E50E24DCCA9E");
BLEUUID UUID_NUS_CHR_TXD("6E400003-B5A3-F393-E0A9-E50E24DCCA9E");
BLEService *server_NordicUart_Service;
BLECharacteristic *server_NUS_Rxd_Chr;        // Write No Response (Receiving Data)
BLECharacteristic *server_NUS_Txd_Chr;        // Read Notify (Sending Data)
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

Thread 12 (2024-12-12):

NimBLE version 2 is disruptive!

Berg0162, 2024-12-12:
The new NimBLE version 2 is disruptive for all existing code. It has a very large number of code breaking changes! Any existing code that is developed with version NimBLE 1.4.3 (or older) will no longer compile, when NimBLE version 2 is installed!

**Keep NimBLE version 1.4.3 installed in your Arduino IDE, do not install NimBLE version 2!**

**Meanwhile: version 1.4.3 works fine!**

**A new repository with redesigned ESP32 code has been published to accommodate for NimBLE-Arduino 2.x, checkout: [Simcline-V2](https://github.com/Berg0162/Simcline-V2)**<br>

Closed 2025-05-30.

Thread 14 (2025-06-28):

Neo 2T test failed

Fukkie-S, 2025-06-28:
Hoi Jörgen,

Ik heb een 2e hands Tacx Neo 2T gekocht en probeer mijn simcline weer aan de praat te krijgen. Ik zag dat je inmiddels nimBLE 2.0 geintegreerd hebt aan de code dus ik heb eerst mijn Arduino bieb geupdate en daarna de mappen uit je Github gedownload en geinstalleerd op mijn laptop. Zonder verdere wijzigingen aan de Feather V2 heb ik daarna je code esp32_Test_Tacx_FE-C_over_BLE_v20.ino ingeladen en ben hoopvol gaan testen. Helaas blijf ik hangen op het feit dat Simcline geen bluetooth verbinding kan krijgen met de Tacx. De firmware van de Tacx Neo is overigens 2.6, de laatste versie dus.

Wat ik heb gedaan is alle bluetooth apparaten uit de buurt gezet. Bluetooth van de laptop uitgezet en via USB verbinding gemaakt met Simcline. Daarna de Tacx Neo van stroom voorzien. Zie outputdump voor de data die ik daarna zag.

Ik heb ook nog getest met nimBLE 2.3.0 ipv 2.3.1 maar dat gaf geen  resultaat. Verbinding maken met Garmin Trainer App is geen probleem ook de Simcline compagnion app ziet de Tacx Neo alvorens de verbinding is gemaakt met Simcline.

Heb jij een hint waarmee ik verder kan zoeken waarom de Tacx Neo 2T niet wil verbinden? Heeft Garmin de laatste firmware gesaboteerd?

Groetjes,

Jan-Willem

08:48:54.520 -> >>> Failed to connect Peripheral with Tacx FE-C Service!
08:48:54.520 -> Client Restarts Scanning for Server Device with Tacx FE-C Service!
08:48:54.574 -> BLE Advertised Device found: Name: Tacx Neo 2T 25596, Address: d2:c2:f2:42:97:ba, appearance: 1152, serviceUUID: 0x1818
08:48:54.590 -> Service Data:
08:48:54.590 -> UUID: 0xfc82, Data:
08:48:55.355 -> >>> Failed to connect Peripheral with Tacx FE-C Service!
08:48:55.355 -> Client Restarts Scanning for Server Device with Tacx FE-C Service!
08:48:55.700 -> Client Disconnected from Server device with Name: [] Mac Address: [00:00:00:00:00:00]!
08:48:55.733 -> Client Restarts Scanning for Server Device with Tacx FE-C Service!
08:48:55.733 -> BLE Advertised Device found: Name: Tacx Neo 2T 25596, Address: d2:c2:f2:42:97:ba, appearance: 1152, serviceUUID: 0x1818
08:48:55.733 -> Service Data:
08:48:55.774 -> UUID: 0xfc82, Data:
08:49:26.746 -> >>> Failed to connect Peripheral with Tacx FE-C Service!
08:49:26.746 -> Client Restarts Scanning for Server Device with Tacx FE-C Service!
08:49:26.799 -> BLE Advertised Device found: Name: Tacx Neo 2T 25596, Address: d2:c2:f2:42:97:ba, appearance: 1152, serviceUUID: 0x1818
08:49:26.799 -> Service Data:
08:49:26.799 -> UUID: 0xfc82, Data:

Tools config
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

Fukkie-S, 2025-06-28:
Ik zie net dat je een V2 hebt gepubliceerd. Ik ga daar eerst mee aan de gang. Sorry voor het storen.

Groetjes Jan-Willem

Berg0162, 2025-06-28:
Best Jan-Willem,
_Tacx Neo 2T_ is **geen** (!) "legacy" Tacx maar een moderne die netjes **FTMS** ondersteunt.... Het lijkt erop dat de _Tacx Neo 2T_ die jij hebt niet langer "ANT+ FE-C over Bluetooth" ondersteunt en dat ligt ook wel voor de hand!
**Simcline-V2** is inderdaad de bibliotheek die je moet gebruiken in dit geval en kies dan wel voor de setting: **ENABLE_FTMS**!

Fukkie-S, 2025-06-28:
Sluit deze maar, Jörgen. We gaan bij de andere verder. Dank voor je snelle reactie.

Berg0162, 2025-06-29:
Ik heb nog eens naar de code gekeken van `esp32_Test_Tacx_FE-C_over_BLE_v20.ino` en het lijkt er toch echt op dat de BLE service: _ANT+ FE-C over Bluetooth_ wel degelijk wordt gevonden, anders had de code geen poging gedaan om een BLE connectie tot stand te brengen met de **Neo2T trainer** ..... Dat het niet lukt is hoogstwaarchijnlijk te wijten aan het feit dat de **Neo2T trainer** al geconnect was (!) met een andere controlling App. Zorg ervoor dat er geen competitie is met andere _controllers_ of _clients_ tijdens het connecten met de trainer!

Closed 2025-06-29.

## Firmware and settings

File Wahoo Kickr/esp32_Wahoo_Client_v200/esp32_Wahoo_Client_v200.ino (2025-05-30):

/*********************************************************************
 This is programming code for ESP32 Espressif Wroom boards
 
      Tested with Adafruit Feather ESP32 V2 a.k.a. Huzzah
 
 The code uses heavily the supplied ESP32 NimBLE libraries !!          
    see: https://github.com/h2zero/NimBLE-Arduino NimBLE Version 2.0
 Many have invested time and resources providing open source code!
 
        MIT license, check LICENSE for more information
        All text must be included in any redistribution
*********************************************************************/

/* 
 *  This Adafruit Feather ESP32 V2 code scans for the CPS + Wahoo Char
 *  that the trainer is advertising, it tries to connect and then 
 *  enables .....
 *  
 *  Requirements: Wahoo trainer and an ESP32 board
 *  1) Upload and Run this code on ESP32 board
 *  2) Start the Serial Monitor to catch verbose debugging and data info
 *  3) Power ON/Wake UP trainer -> do NOT connect with other devices
 *  4) Trainer and ESP32 board should successfully pair or disconnect...
 *  5) Keep the Serial Monitor visible on top of all windows 
 *  6) Move the trainer pedals and notice/feel changes in resistance...
 *     The Client sends Resistance Parameters to the Trainer
 *  7) Inspect the info presented by Serial Monitor.....
 *  
 */
/*
Version 1.0
Changed device identification naming to a simpler scheme: SIM32 or SIM52 instead of <SIM DevName>
NimBLE registerForNotify() has been deprecated and is replaced with subscribe() / unsubscribe()
Version 2.0
Revisited the code to improve its logic, robustness and working. Further adapted the code at 
numerous places to conform with NimBLE Version 2.0
*/

#include <algorithm>

// -------------------------------------------------------------------------------------------
// COMPILER DIRECTIVE to allow/suppress DEBUG messages that help debugging...
// Uncomment general "#define DEBUG" to activate
#define DEBUG
// Include these debug utility macros in all cases!
#include "DebugUtils.h"
//
#ifdef DEBUG
//#define DEBUG_CP_MEASUREMENT  // If defined allows for presentation of Cycling Power Data
//#define DEBUG_CSC_MEASUREMENT // If defined allows for presentation of Cadence & Speed Data
#endif
// --------------------------------------------------------------------------------------------

#define BLE_APPEARANCE_GENERIC_CYCLING   1152

/******************************* O P T I O N A L ********************************** 
   To enable more meaningful text messages, please un-comment inside "nimconfig.h"
   (../arduino/libraries/NimBLE-Arduino/src/nimconfig.h) at the following entry:
***********************************************************************************
 ** @brief Un-comment to see NimBLE host return codes as text debug log messages.
 *  Uses approx. 7kB of flash memory.
 *
//#define CONFIG_NIMBLE_CPP_ENABLE_RETURN_CODE_TEXT
*/

#include <NimBLEDevice.h>

// We need this for setting the Server-side Generic Access Char's --> Appearance and DeviceName
#include <nimble/nimble/host/services/gap/include/services/gap/ble_svc_gap.h>

#define THISDEVICENAME "SIM32" // Shortname 

// Client Generic Access --------------------------------------------------------------
#define UUID16_SVC_GENERIC_ACCESS                             NimBLEUUID((uint16_t)0x1800)
#define UUID16_CHR_DEVICE_NAME                                NimBLEUUID((uint16_t)0x2A00)
#define UUID16_CHR_APPEARANCE                                 NimBLEUUID((uint16_t)0x2A01)
#define UUID16_CHR_PERIPHERAL_PREFERRED_CONNECTION_PARAMETERS NimBLEUUID((uint16_t)0x2A04)
#define UUID16_CHR_CENTRAL_ADDRESS_RESOLUTION                 NimBLEUUID((uint16_t)0x2AA6)
static NimBLERemoteService* pRemote_GenericAccess_Service;
static NimBLERemoteCharacteristic* pRemote_GA_Appearance_Chr; // Read
uint16_t client_GA_Appearance_Value = BLE_APPEARANCE_GENERIC_CYCLING;  // Default decimal: 1152 -> Generic Cycling
static NimBLERemoteCharacteristic* pRemote_GA_DeviceName_Chr;// Read, Write
std::string client_GA_DeviceName_Str = THISDEVICENAME;

// Client Service Device Information --------------------------------------------------
#define UUID16_SVC_DEVICE_INFORMATION                         NimBLEUUID((uint16_t)0x180A)
#define UUID16_CHR_MODEL_NUMBER_STRING                        NimBLEUUID((uint16_t)0x2A24)
#define UUID16_CHR_SERIAL_NUMBER_STRING                       NimBLEUUID((uint16_t)0x2A25)
#define UUID16_CHR_MANUFACTURER_NAME_STRING                   NimBLEUUID((uint16_t)0x2A29)
/*
#define UUID16_CHR_FIRMWARE_REVISION_STRING                   NimBLEUUID((uint16_t)0x2A26)
#define UUID16_CHR_HARDWARE_REVISION_STRING                   NimBLEUUID((uint16_t)0x2A27)
#define UUID16_CHR_SOFTWARE_REVISION_STRING                   NimBLEUUID((uint16_t)0x2A28)
*/
static NimBLERemoteService* pRemote_DeviceInformation_Service; 
static NimBLERemoteCharacteristic* pRemote_DIS_ManufacturerName_Chr;   // Read
std::string client_DIS_Manufacturer_Str;
static NimBLERemoteCharacteristic* pRemote_DIS_ModelNumber_Chr;        // Read
std::string client_DIS_ModelNumber_Str;
static NimBLERemoteCharacteristic* pRemote_DIS_SerialNumber_Chr;       // Read
std::string client_DIS_SerialNumber_Str;
// -------------------------------------------------------------------------------------

#define MAXPAYLOAD 20

/* Cycling Power Service ---------------------------------------------------------------
 * CP Service: 0x1818  
 * CP Characteristic: 0x2A63 (Measurement)    Mandatory
 * CP Characteristic: 0x2A65 (Feature)        Mandatory
 * CP Characteristic: 0x2A5D (Location)       Optional
 * CP Characteristic: 0x2A66 (Control Point)  Optional
 */
#define UUID16_SVC_CYCLING_POWER                NimBLEUUID((uint16_t)0x1818)
#define UUID16_CHR_CYCLING_POWER_MEASUREMENT    NimBLEUUID((uint16_t)0x2A63)
#define UUID16_CHR_CYCLING_POWER_FEATURE        NimBLEUUID((uint16_t)0x2A65)
#define UUID16_CHR_SENSOR_LOCATION              NimBLEUUID((uint16_t)0x2A5D)
#define UUID16_CHR_CYCLING_POWER_CONTROL_POINT  NimBLEUUID((uint16_t)0x2A66)

static NimBLERemoteService* pRemote_CyclingPower_Service;
static NimBLERemoteCharacteristic* pRemote_CP_Measurement_Chr;    // Notify, Read
static NimBLERemoteCharacteristic* pRemote_CP_Feature_Chr;        // Read
uint32_t client_CP_Feature_Flags = 0;
static NimBLERemoteCharacteristic* pRemote_CP_Location_Chr;       // Read
uint8_t client_CP_Location_Value = 0; // UINT8
/* ---------------------------------------------------------------------------------------------------------------
 * Wahoo Proprietary Control Point Characteristic
 * ---------------------------------------------------------------------------------------------------------------*/
// Proprietary Wahoo Trainer Control Point Characteristic is part of the Cycling Power Service !
static NimBLEUUID UUID16_CHR_WAHOO_CONTROL_POINT("A026E005-0A7D-4AB3-97FA-F1500F9FEB8B");
static NimBLERemoteCharacteristic* pRemote_Wahoo_ControlPoint_Chr; //  Wahoo Control Point Indicate, Write

// client_CPS Wahoo Trainer Operation Codes in Decimal
const uint8_t unlock                     = 32;
/*
const uint8_t setResistanceMode          = 64;
const uint8_t setStandardMode            = 65;
const uint8_t setErgMode                 = 66;
const uint8_t setSimMode                 = 67;
const uint8_t setSimCRR                  = 68;
const uint8_t setSimWindResistance       = 69;
const uint8_t setSimGrade                = 70;
const uint8_t setSimWindSpeed            = 71;
const uint8_t setWheelCircumference      = 72;
*/
const uint8_t unlockCommand[3] = {unlock, 0xEE, 0xFC}; // Unlock codes

const uint8_t client_CP_Feature_Len = 20; // Num. of Feature elements
const char* client_CP_Feature_Str[client_CP_Feature_Len] = { 
      "Pedal power balance supported",
      "Accumulated torque supported",
      "Wheel revolution data supported",
      "Crank revolution data supported",
      "Extreme magnitudes supported",
      "Extreme angles supported",
      "Top/bottom dead angle supported",
      "Accumulated energy supported",
      "Offset compensation indicator supported",
      "Offset compensation supported",
      "Cycling power measurement characteristic content masking supported",
      "Multiple sensor locations supported",
      "Crank length adj. supported",
      "Chain length adj. supported",
      "Chain weight adj. supported",
      "Span length adj. supported",
      "Sensor measurement context",
      "Instantaineous measurement direction supported",
      "Factory calibrated date supported",
      "Enhanced offset compensation supported" };

const uint8_t client_Sensor_Location_Str_Len = 17;       
const char* client_Sensor_Location_Str[client_Sensor_Location_Str_Len] = { "Other", "Top of shoe", 
    "In shoe", "Hip", "Front wheel", "Left crank", "Right crank", "Left pedal", "Right pedal", "Front hub", 
    "Rear dropout", "Chainstay", "Rear wheel", "Rear hub", "Chest", "Spider", "Chain ring"};

/*------------------------------------------------ OPTIONAL ---------------------------------------
 * Cycling Speed and Cadence Service
 * CSC Service:   0x1816 
 * CSC Measurement Characteristic:  0x2A5B
 * CSC Feature Characteristic:      0x2A5C  
 */
#define UUID16_SVC_CYCLING_SPEED_AND_CADENCE  NimBLEUUID((uint16_t)0x1816)
#define UUID16_CHR_CSC_MEASUREMENT            NimBLEUUID((uint16_t)0x2A5B)
#define UUID16_CHR_CSC_FEATURE                NimBLEUUID((uint16_t)0x2A5C)
// PM   UUID16_CHR_SENSOR_LOCATION shared with Cycling Power Service
static NimBLERemoteService* pRemote_CyclingSpeedCadence_Service;
static NimBLERemoteCharacteristic* pRemote_CSC_Measurement_Chr;         // Notify, Read
static NimBLERemoteCharacteristic* pRemote_CSC_Feature_Chr;             // Read
const uint8_t CSC_FEATURE_FIXED_DATALEN = 2; // UINT16
uint16_t client_CSC_Feature_Flags = 0;
static NimBLERemoteCharacteristic* pRemote_CSC_Location_Chr;             // Read
uint8_t client_CSC_Location_Value = 0; 

/* CSC Control Point Characteristic:0x2A55 --->  not implemented
// CSC Control Point op codes 
#define     SC_CP_OP_SET_CUMULATIVE_VALUE           1
#define     SC_CP_OP_START_SENSOR_CALIBRATION       2
#define     SC_CP_OP_UPDATE_SENSOR_LOCATION         3
#define     SC_CP_OP_REQ_SUPPORTED_SENSOR_LOCATIONS 4
#define     SC_CP_OP_RESPONSE                       16
// CSC Control Point response values
#define     SC_CP_RESPONSE_SUCCESS                  1
#define     SC_CP_RESPONSE_OP_NOT_SUPPORTED         2
#define     SC_CP_RESPONSE_INVALID_PARAM            3
#define     SC_CP_RESPONSE_OP_FAILED                4
*/

/*CSC Measurement flags*/
#define     CSC_MEASUREMENT_WHEEL_REV_PRESENT       0x01
#define     CSC_MEASUREMENT_CRANK_REV_PRESENT       0x02

/* CSC Feature flags */
#define     CSC_FEATURE_WHEEL_REV_DATA              0x01
#define     CSC_FEATURE_CRANK_REV_DATA              0x02
#define     CSC_FEATURE_MULTIPLE_SENSOR_LOC         0x04

const uint8_t client_CSC_Feature_Len = 3;
const char* client_CSC_Feature_Str[client_CSC_Feature_Len] = {"Wheel rev supported", "Crank rev supported", \
                                                                "Multiple locations supported"};
// --------------------------------------------------------------------------------------
static NimBLEClient* pClient_Wahoo;
static const NimBLEAdvertisedDevice* trainerDevice;
static NimBLEScan* pNimBLEScan;

static boolean doClientConnectCall = false;
static boolean clientIsConnected = false;
static uint8_t clientPeerAddress[6] = {};
static std::string clientPeerName;
static boolean RestartScanningOnDisconnect = false;
static boolean hasConnectPassed = false;

// Values used to enable or disable notifications/indications
const bool indications = false;  //false as first argument to subscribe to indications instead of notifications
const bool notifications = true; //true as first argument to subscribe to notifications
// ---------------------------------------------------------------------------------------
#define CONTROL_POINT_TIME_SPAN 3000    // Time span for sending Wahoo Control Point data
unsigned long TimeInterval = 0;
float Grade = 0.0;

// Client Connect and Disconnect callbacks defined
class client_Connection_Callbacks : public NimBLEClientCallbacks {
  void onConnect(NimBLEClient* pClient);
  void onConnectFail(NimBLEClient* pClient, int reason);
  void onDisconnect(NimBLEClient* pClient, int reason);
  bool onConnParamsUpdateRequest(NimBLEClient* pClient, const ble_gap_upd_params *params);  
};

void ConvertMacAddress(char *fullAddress, uint8_t addr[6], bool NativeFormat)
{ // Display byte by byte in HEX 
  if(NativeFormat) { // Unaltered: representation
    sprintf(fullAddress, "%02X:%02X:%02X:%02X:%02X:%02X", addr[0], addr[1], addr[2], \
      addr[3], addr[4], addr[5], HEX);   
  } else { // Altered: in reversed order
    sprintf(fullAddress, "%02X:%02X:%02X:%02X:%02X:%02X", addr[5], addr[4], addr[3], \
      addr[2], addr[1], addr[0], HEX);       
  }
}
// Forward declarations
void client_Start_Scanning(void);
void clientSubscribeToAll(void);
bool ClientConnectServer(void);

void setup() {
#ifdef DEBUG
  Serial.begin(115200);
  while (!Serial) delay(10); 
  Serial.flush();
  delay(1000); // Give Serial I/O time to settle
#endif

  DEBUG_PRINTLN("");
  DEBUG_PRINTLN("ESP32 BLE Wahoo Client/Central: CPS + Wahoo and CSC (optional)");
  DEBUG_PRINTLN("------------------------ Version 02.0 ------------------------");
  DEBUG_PRINTF("Device Name: %s with NimBLE Version 2.0\n", THISDEVICENAME);
  delay(200);
#ifdef CONFIG_NIMBLE_CPP_ENABLE_RETURN_CODE_TEXT
  DEBUG_PRINTLN("CONFIG_NIMBLE_CPP_ENABLE_RETURN_CODE_TEXT enabled!");
#endif
  client_Start_Scanning();
} // End of setup.

void client_Connection_Callbacks::onConnect(NimBLEClient* pClient) {
    NimBLEAddress MyAddress = trainerDevice->getAddress();
    clientPeerName = trainerDevice->getName().c_str();
    memcpy(&clientPeerAddress, MyAddress.getBase()->val, 6);
    uint8_t addressType = MyAddress.getBase()->type; 
#ifdef DEBUG
    DEBUG_PRINT("Client Connection Parameters -> ");
    uint16_t max_payload = pClient_Wahoo->getMTU();
    //DEBUG_PRINTF("Max Transmission Unit: [%d] ", max_payload);
    uint16_t clientConnectionInterval = pClient_Wahoo->getConnInfo().getConnInterval();
    DEBUG_PRINTF("Interval: [%d] ", clientConnectionInterval);
    uint16_t clientConnectionLatency = pClient_Wahoo->getConnInfo().getConnLatency();
    DEBUG_PRINTF("Latency: [%d] ", clientConnectionLatency);
    uint16_t clientConnectionSupTimeout = pClient_Wahoo->getConnInfo().getConnTimeout();
    DEBUG_PRINTF("Supervision Timeout: [%d]\n", clientConnectionSupTimeout);
    char fullMacAddress[18] = {}; //
    ConvertMacAddress(fullMacAddress, clientPeerAddress, false); // true -> Native Format
    DEBUG_PRINTF("ESP32 Client connects to Server device with Name: [%s] MAC Address: [%s][%d] MTU: [%d]\n", \
                    clientPeerName.c_str(), fullMacAddress, addressType, max_payload); 
#endif       
    doClientConnectCall = true;    
  };

void client_Connection_Callbacks::onConnectFail(NimBLEClient* pClient, int reason) {
#ifdef CONFIG_NIMBLE_CPP_ENABLE_RETURN_CODE_TEXT
    DEBUG_PRINTF("Connection failure -> [%d][%s]\n", reason, NimBLEUtils::returnCodeToString(reason));
#else
    DEBUG_PRINTLN("");
#endif
};

bool client_Connection_Callbacks::onConnParamsUpdateRequest(NimBLEClient* pClient, const ble_gap_upd_params *params) {
    DEBUG_PRINTLN("Client Connection Parameter Update Request!");
    /** Minimum value for connection interval in 1.25ms units */
    uint16_t clientConnectionMinInterval = params->itvl_min;
    DEBUG_PRINTF("Min Interval: [%d]\n", clientConnectionMinInterval);
    /** Maximum value for connection interval in 1.25ms units */
    uint16_t clientConnectionMaxInterval = params->itvl_max;
    DEBUG_PRINTF("Max Interval: [%d]\n", clientConnectionMaxInterval);
    /** Connection latency */
    uint16_t clientConnectionLatency = params->latency;
    DEBUG_PRINTF("Latency: [%d]\n", clientConnectionLatency);
    /** Supervision timeout in 10ms units */
    uint16_t clientConnectionSupTimeout = params->supervision_timeout;
    DEBUG_PRINTF("Sup. Timeout: [%d]\n", clientConnectionSupTimeout);
    /** Minimum length of connection event in 0.625ms units */
    uint16_t clientMinLenEvent = params->min_ce_len;
    DEBUG_PRINTF("Min Length Event: [%d]\n", clientMinLenEvent);
    /** Maximum length of connection event in 0.625ms units */
    uint16_t clientMaxLenEvent = params->max_ce_len;  
    DEBUG_PRINTF("Max Length Event: [%d]\n", clientMaxLenEvent);
    return true; // That is OK!  
};

void client_Connection_Callbacks::onDisconnect(NimBLEClient* pClient, int reason) {
    clientIsConnected = false;
    char fullMacAddress[18] = {}; //
    ConvertMacAddress(fullMacAddress, clientPeerAddress, false); // true -> Native Format
    DEBUG_PRINTF("Client Disconnected from Server device with Name: [%s] Mac Address: [%s]",  \
                    clientPeerName.c_str(), fullMacAddress);
#ifdef CONFIG_NIMBLE_CPP_ENABLE_RETURN_CODE_TEXT
    DEBUG_PRINTF(" -> [%d][%s]\n", reason, NimBLEUtils::returnCodeToString(reason));
#else
    DEBUG_PRINTLN("");
#endif
    RestartScanningOnDisconnect = true;
};

bool client_DeviceInformation_Connect(void)
{
    // If Device Information is not found then go on.... NOT FATAL !
    pRemote_DeviceInformation_Service = pClient_Wahoo->getService(UUID16_SVC_DEVICE_INFORMATION);    
    if ( pRemote_DeviceInformation_Service == nullptr ) {
      DEBUG_PRINT(F("Device Information Service: NOT Found!\n"));
      return true;
    }
      DEBUG_PRINT(F("Client Device Information Service: Found!\n"));
      pRemote_DIS_ManufacturerName_Chr = pRemote_DeviceInformation_Service->getCharacteristic(UUID16_CHR_MANUFACTURER_NAME_STRING);  
      if ( pRemote_DIS_ManufacturerName_Chr != nullptr ) {
          if(pRemote_DIS_ManufacturerName_Chr->canRead()) {
            client_DIS_Manufacturer_Str = pRemote_DIS_ManufacturerName_Chr->readValue();
            DEBUG_PRINTF(" -> Client Reads Manufacturer Name: [%s]\n", client_DIS_Manufacturer_Str.c_str());
          }            
      }     
      pRemote_DIS_ModelNumber_Chr = pRemote_DeviceInformation_Service->getCharacteristic(UUID16_CHR_MODEL_NUMBER_STRING);       
      if ( pRemote_DIS_ModelNumber_Chr != nullptr ) {
          if(pRemote_DIS_ModelNumber_Chr->canRead()) {
            client_DIS_ModelNumber_Str = pRemote_DIS_ModelNumber_Chr->readValue();
            DEBUG_PRINTF(" -> Client Reads Model Number:      [%s]\n", client_DIS_ModelNumber_Str.c_str());
          }
      }  
      pRemote_DIS_SerialNumber_Chr = pRemote_DeviceInformation_Service->getCharacteristic(UUID16_CHR_SERIAL_NUMBER_STRING);       
      if ( pRemote_DIS_SerialNumber_Chr != nullptr ) {
          if(pRemote_DIS_SerialNumber_Chr->canRead()) {
            client_DIS_SerialNumber_Str = pRemote_DIS_SerialNumber_Chr->readValue();
            DEBUG_PRINTF(" -> Client Reads Serial Number:     [%s]\n", client_DIS_SerialNumber_Str.c_str());
          }
      }       
  return true;    
}

bool client_GenericAccess_Connect(void)
{
    // If Generic Access is not found then go on.... NOT FATAL !
    pRemote_GenericAccess_Service = pClient_Wahoo->getService(UUID16_SVC_GENERIC_ACCESS);    
    if ( pRemote_GenericAccess_Service == nullptr ) {
      DEBUG_PRINTLN(F("Client Generic Access: NOT Found!"));
      return true;
    }
    DEBUG_PRINTLN("Client Generic Access: Found!");
    pRemote_GA_DeviceName_Chr = pRemote_GenericAccess_Service->getCharacteristic(UUID16_CHR_DEVICE_NAME);  
      if ( pRemote_GA_DeviceName_Chr != nullptr ) {
          if(pRemote_GA_DeviceName_Chr->canRead()) {
            client_GA_DeviceName_Str = pRemote_GA_DeviceName_Chr->readValue();
            DEBUG_PRINTF(" -> Client Reads Device Name:   [%s]\n", client_GA_DeviceName_Str.c_str());
          }            
      }     
      pRemote_GA_Appearance_Chr = pRemote_GenericAccess_Service->getCharacteristic(UUID16_CHR_APPEARANCE);       
      if ( pRemote_GA_Appearance_Chr != nullptr ) {
          if(pRemote_GA_Appearance_Chr->canRead()) {
            client_GA_Appearance_Value = pRemote_GA_Appearance_Chr->readValue<uint16_t>();
            DEBUG_PRINTF(" -> Client Reads Appearance:    [%d]\n", client_GA_Appearance_Value);
          }
      }     
    return true;     
}
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
void loop() {
  // If the flag "doClientConnectCall" is true, we have found the desired BLE server!
  // Once we are connected and ALL is set the clientIsConnected flag is set true.
  if (doClientConnectCall == true) {
    if( !ClientConnectServer() ) {
        DEBUG_PRINTLN(">>> Failed to connect Peripheral (Wahoo)!");
        NimBLEDevice::deleteClient(pClient_Wahoo); // Delete client object and clear from list
        pClient_Wahoo = nullptr;   // Clear to null
        if(!hasConnectPassed) RestartScanningOnDisconnect = true; 
    }
    doClientConnectCall = false;
  } // doClientConnectCall

  if (clientIsConnected) {
    // If time is there, send test Simulation Parameters to the Wahoo Control Point...
    if(millis() > TimeInterval) {
        Grade += 1.0;     // Increase the simulated road grade
        Set_SimGrade(Grade); 
        if (Grade > 9.0) {
            Set_SimMode(); // Repeat every 10 events
            Grade = 0.0;
        }
        TimeInterval = millis() + CONTROL_POINT_TIME_SPAN;
    } // TimeInterval
  } else { // client is NOT connected check for (re)start scanning
    if(RestartScanningOnDisconnect) {
        pNimBLEScan->clearResults();   // delete results from NimBLEScan buffer to release memory    
        DEBUG_PRINTLN("Client Restarts Scanning for Server Device (Wahoo) with CPS!");
        RestartScanningOnDisconnect = false;        
        pNimBLEScan->start(0, false);
    } 
  }      
} // End of loop

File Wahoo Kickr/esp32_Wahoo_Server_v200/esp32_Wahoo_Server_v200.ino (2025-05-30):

/*********************************************************************
 This is programming code for ESP32 Espressif Wroom boards
 
      Tested with Adafruit Feather ESP32 V2 a.k.a. Huzzah
 
 The code uses heavily the supplied ESP32 NimBLE libraries !!          
    see: https://github.com/h2zero/NimBLE-Arduino NimBLE Version 2.x
 Many have invested time and resources providing open source code!
 
        MIT license, check LICENSE for more information
        All text must be included in any redistribution
*********************************************************************/

/* 
 *  This Adafruit ESP32 Huzzah V2 tested code advertises and enables the relevant 
 *  Cycling Trainer Services: CPS + Wahoo proprietary Characteristic and CSC (optional).
 *  It allows to connect to Cycling apps like Zwift (aka Client or Central)!
 *  It simulates a connected Cycling Trainer and in BLE terms it is a Server or 
 *  or in BlueFruit BLE library terms it is a Peripheral!
 *  Requirements: Zwift app or alike and an ESP32 board
 *  1) Upload and Run this code on the ESP32
 *  2) Start the Serial Monitor to catch debugging info
 *  3) Start Zwift and wait for the Devices Pairing Screen
 *  4) Unpair all previously paired devices
 *  5) Search on Zwift pairing screens for the ESP32 a.k.a. <SIM32>
 *  6) Pair: Power Source, Cadence (optional) and Resistance one after another with <SIM32>
 *  7) Start a default Zwift ride or any ride you wish
 *     No need for you to do work on the trainer!
 *  8) Make Serial Monitor visible on top of the Zwift window 
 *  9) Inspect the info presented by Serial Monitor
 * 10) Notice how your avatar is riding the route all by itself...
 *  
 * This device is identified with the name <SIM32>. You will see this only when connecting to Zwift on the 
 * pairing screens! Notice: Zwift extends device names with additional numbers for identification!
 *
 */
/*
Version 1.0
Changed device identification naming to a simpler scheme: SIM32 or SIM52 instead of <SIM DevName>
Version 2.0
Adapted code at numerous places to conform with NimBLE Version 2.0 
*/

// -------------------------------------------------------------------------------------------
// COMPILER DIRECTIVE to allow/suppress DEBUG messages that help debugging...
// Uncomment general "#define DEBUG" to activate
#define DEBUG
// Include these debug utility macros in all cases!
#include "DebugUtils.h"
// --------------------------------------------------------------------------------------------

#define BLE_APPEARANCE_GENERIC_CYCLING   1152

#include <NimBLEDevice.h>
#include <nimble/nimble/host/services/gap/include/services/gap/ble_svc_gap.h>

#define THISDEVICENAME "SIM32" // Shortname 

// Defined globally
const uint8_t MAX_PAYLOAD = 20; // Max 20 byte data size for single packet BLE transfer
NimBLEServer* pServer;
NimBLEAdvertising* pAdvertising;

uint8_t serverPeerAddress[6];
bool serverIsConnected = false;
uint16_t serverConnectionHandle = BLE_HS_CONN_HANDLE_NONE;

// ------------------------------------------------------------------------------------
// Client Generic Access Service-------------------------------------------------------
// -----------------------------------------------------------------------------------
// Server Generic Access variables
uint16_t client_GA_Appearance_Value = BLE_APPEARANCE_GENERIC_CYCLING;  // decimal: 1152 -> Generic Cycling
// Set the advertised device name
std::string client_GA_DeviceName_Str = THISDEVICENAME;
// ------------------------------------------------------------------------------------

// ------------------------------------------------------------------------------------
// Client Service Device Information 
// ------------------------------------------------------------------------------------
#define UUID16_SVC_DEVICE_INFORMATION                         BLEUUID((uint16_t)0x180A)
#define UUID16_CHR_MODEL_NUMBER_STRING                        BLEUUID((uint16_t)0x2A24)
#define UUID16_CHR_SERIAL_NUMBER_STRING                       BLEUUID((uint16_t)0x2A25)
#define UUID16_CHR_MANUFACTURER_NAME_STRING                   BLEUUID((uint16_t)0x2A29)
/*
#define UUID16_CHR_FIRMWARE_REVISION_STRING                   BLEUUID((uint16_t)0x2A26)
#define UUID16_CHR_HARDWARE_REVISION_STRING                   BLEUUID((uint16_t)0x2A27)
#define UUID16_CHR_SOFTWARE_REVISION_STRING                   BLEUUID((uint16_t)0x2A28)
*/
NimBLEService *server_DeviceInformation_Service;
NimBLECharacteristic *server_DIS_ModelNumber_Chr;       // Read
std::string client_DIS_ModelNumber_Str = "Kickr";
NimBLECharacteristic *server_DIS_SerialNumber_Chr;      // Read
std::string client_DIS_SerialNumber_Str = "123";
NimBLECharacteristic *server_DIS_ManufacturerName_Chr;  // Read
std::string client_DIS_Manufacturer_Str = "Wahoo Fitness";
/*
NimBLECharacteristic *server_DIS_Firmware_Chr;          // Read
std::string client_DIS_Firmware_Str = "12";
NimBLECharacteristic *server_DIS_Hardware_Chr;          // Read
std::string client_DIS_Hardware_Str = "1";
NimBLECharacteristic *server_DIS_Software_Chr;          // Read
std::string client_DIS_Software_Str = "0";
*/
// -------------------------------------------------------------------------------------

/* NORDIC UART SERVICE a.k.a. NUS
 * NUS Service: 6E400001-B5A3-F393-E0A9-E50E24DCCA9E
 * NUS RXD    : 6E400002-B5A3-F393-E0A9-E50E24DCCA9E
 * NUS TXD    : 6E400003-B5A3-F393-E0A9-E50E24DCCA9E
 */
static BLEUUID UUID_NUS_SERVICE("6E400001-B5A3-F393-E0A9-E50E24DCCA9E");
static BLEUUID UUID_NUS_CHR_RXD("6E400002-B5A3-F393-E0A9-E50E24DCCA9E");
static BLEUUID UUID_NUS_CHR_TXD("6E400003-B5A3-F393-E0A9-E50E24DCCA9E");
NimBLEService *server_NordicUart_Service; 
NimBLECharacteristic *server_NUS_Rxd_Chr;        // Write No Response (Receiving Data)
NimBLECharacteristic *server_NUS_Txd_Chr;        // Read Notify (Sending Data)

/* Cycling Power Service -------------------------------------------------------------------------------------------
 * CP Service: 0x1818  
 * CP Characteristic: 0x2A63 (Measurement)
 * CP Characteristic: 0x2A65 (Feature)
 * CP Characteristic: 0x2A5D (Location)
 * CP Characteristic: 0x2A66 (Control Point) -> Not implemented
 */
#define UUID16_SVC_CYCLING_POWER                              BLEUUID((uint16_t)0x1818)
#define UUID16_CHR_CYCLING_POWER_MEASUREMENT                  BLEUUID((uint16_t)0x2A63)
//#define UUID16_CHR_CYCLING_POWER_VECTOR                       BLEUUID((uint16_t)0x2A64)
#define UUID16_CHR_CYCLING_POWER_FEATURE                      BLEUUID((uint16_t)0x2A65)
//#define UUID16_CHR_CYCLING_POWER_CONTROL_POINT                BLEUUID((uint16_t)0x2A66)
#define UUID16_CHR_SENSOR_LOCATION                            BLEUUID((uint16_t)0x2A5D) // shared with CSC
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

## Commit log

2022-11-19 Create FTMS_Client_v012.ino
    Problem solved with wrong parsing of IBData packet for serial print output
2022-11-20 Create FTMS_Client_v013.ino
    Corrected Tot. Distance print out
2022-11-28 Added Freecad File
    Components box + lid
    [Components_Box_Complete_02.FCStd]
2022-12-12 Debug Output Example FTMS Client
    Debug output Sample
2022-12-15 Create FTMS_Client_v027.ino
    Inserted time controlled loop for enabling Notify or Indicate....
2022-12-17 Added new version 028
    Inserted delay to coop with time out
2023-02-23 Reorganized
    Reorganized to make space for ESP32 code
2023-02-26 Added ESP32 version
2023-03-18 New ESP32 version
2023-03-18 Added New ESP32 version
2024-11-30 Update esp32_Wahoo_Simcline_v012.ino
    Critical update
2024-12-08 Update README.md
    Inserted a Q&A about connection problems!
2024-12-08 Update README.md
    Inserted an Q&A about problems when connecting the trainer
2025-03-05 Be aware what NimBLE-Arduino version to install!
2025-05-30 Updated to NimBLE-Arduino version 2.3.0
